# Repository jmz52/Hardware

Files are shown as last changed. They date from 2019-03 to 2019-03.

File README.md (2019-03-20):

# RAMPS-like shield for [black STM32F407VET6](https://wiki.stm32duino.com/index.php?title=STM32F407) board

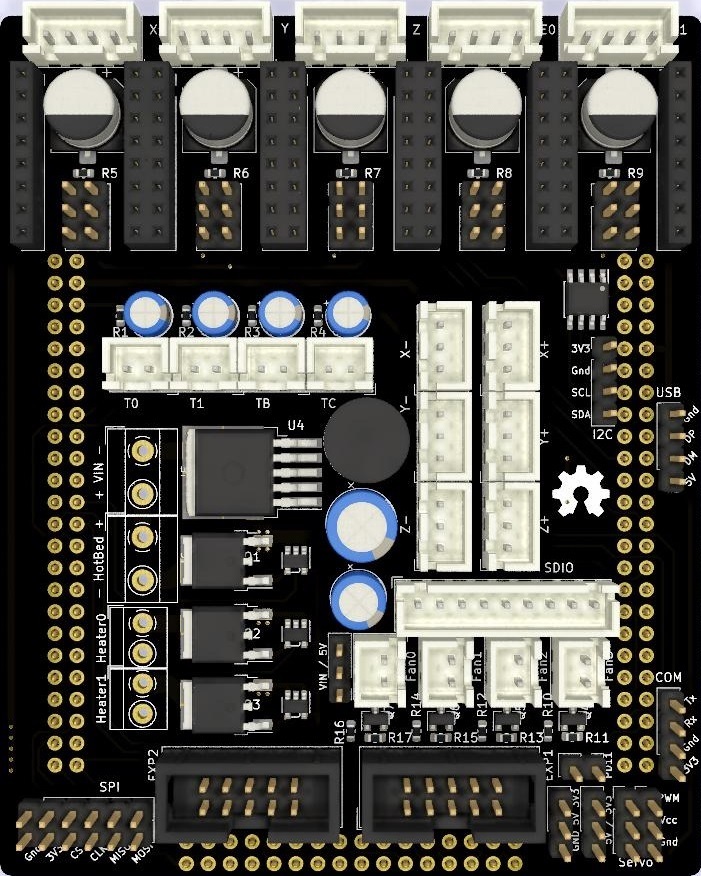
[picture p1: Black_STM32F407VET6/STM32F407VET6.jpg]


__Work-in-progress. Use with caution!__

First public release.
Corrected version of prototype board.

Changelog:
 - Updated pins names on 2x24 connectors and removed 3V3 to GND wire
 - Fixed broken E1_enable wire
 - Added missing wire between CLK pins in SPI connector

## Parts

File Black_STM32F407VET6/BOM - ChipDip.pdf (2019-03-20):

| количество | Ном. номер | цена | | название
Нагреватели | 3 | 9000087082 | 27 | 81 | IRLR8726PBF, Транзистор, N-канал 30В 85А [D-PAK]
| 3 | 9050000043 | 6 | 18 | SN74AHC1G125DBVR, Микросхема 1 Bus Buffer Gate 3-St SN [SOT-23-5]
Вентиляторы | 4 | 9000089114 | 10 | 40 | IRLML0030TRPBF, Транзистор, N-канал 30В 5.3А, [SOT-23]
| 4 | 9000079557 | 0.90 | 3.60 | 0.063Вт 0603 10 Ом, 1%, Чип резистор (SMD)
| 4 | 9000079736 | 0.90 | 3.60 | 0.063Вт 0603 10 кОм, 1%, Чип резистор (SMD)
5V | 1 | 949674977 | 290 | 290 | LM2596S-5.0/NOPB, Импульсный понижающий регулятор напряжения, 5В, 3А, 150кГц [TO-263-5]
| 1 | 9000355356 | 5 | 5 | SS14, Диод Шоттки 1A 40В [SMA / DO-214AC]
| 1 | 51810 | 38 | 38 | RLB0914-470KL, 47 мкГн,, Катушка индуктивности
| 1 | 9000261772 | 8 | | ECAP (К50-35 мини), 100 мкФ, 35 В, 8х7мм, Конденсатор электролитический алюминиевый миниатюрный
| 1 | 484555302 | 7 | | ECAP (К50-35), 220 мкФ, 35 В, 105°C, Конденсатор электролитический алюминиевый
Клеммники | 2 | 3017 | 19 | 38 | ED500V-02P, Клеммник 2-контактный, 5мм
| 2 | 37182 | 25 | 50 | ED350V-02P, Клеммник
Обвязка | 4 | 9000261763 | 5 | 20 | ECAP (К50-35 мини), 10 мкФ, 16 В, 4х7мм, Конденсатор электролитический алюминиевый миниатюрный
термисторов | 4 | 9000079728 | 0.90 | 3.60 | 0.063Вт 0603 4.7 кОм, 1%, Чип резистор (SMD)
Обвязка | 5 | 31139 | 20 | 100 | ECAP SMD, 100 мкФ, 25В, Конденсатор электролитический алюминиевый SMD | для 12 вольт
драйверов | 0 | 821121660 | 19 | 0 | ECAP SMD, 100 мкФ, 50В, Конденсатор электролитический алюминиевый SMD | для 24 вольт
| 5 | 9000079728 | 0.9 | 4.5 | 0.063Вт 0603 4.7 кОм, 1%, Чип резистор (SMD)
| 15 | 38729 | 5 | 75 | MJ-O-6 (DS1027-2 A), Джампер 2.54х6мм 2-контактный открытый
USB | 2 | 9000079564 | 0.90 | 1.80 | 0.063Вт 0603 22 Ом, 1%, Чип резистор (SMD)
I2C | 2 | 9000079728 | 0.90 | 1.80 | 0.063Вт 0603 4.7 кОм, 1%, Чип резистор (SMD)
SPI | 1 | 9000079728 | 0.90 | 0.90 | 0.063Вт 0603 4.7 кОм, 1%, Чип резистор (SMD)
EEPROM | 1 | 9060000150 | 12.00 | 12.00 | M24C64-WMN6TP, Энергонезависимая память, 64 кбит [SO-8]

Разъемы
EXP1/EXP2 | 2 | 62904 | 6 | 12 | BH-10 (DS1013-10S) (IDC-10MS), Вилка на плату прямая 10 конт. 2.54мм
2.54 | 1 | 29417 | 21 | 21 | PBD-40 (DS1023-2X20), Гнездо на плату 2.54мм 2х20 прямое
| 2 | 36056 | 30 | 60 | PBD-50 (DS1023-2x25), Гнездо на плату 2.54мм 2х25 прямое | 2x24 нет в наличии
| 2 | 32562 | 7 | 14 | PBS-8 (DS-1023 -1x 8), Гнездо на плату 2.54мм 1х8 прямое
| 4 | 25097 | 10 | 40 | PBD-16 (DS1023-2x8), Гнездо на плату 2.54мм 2х8 прямое
| 2 | 250743391 | 13 | 26 | PLD-40 (DS-1021- 2x20), Вилка штыревая 2.54мм 2х20 прямая тип1
| 1 | 39606 | 15 | 15 | PLS-40 (DS1021-1x40), Вилка штыревая 2.54мм 1х40 прямая тип1
2.50 | 5 | 33929 | 5 | 25 | CWF-4 (DS1069-4 M), Вилка на плату 2.50мм прямая закрытая
| 6 | 758365295 | 5 | 30 | CWF-3 (DS1069-3 M), Вилка на плату 2.50мм прямая закрытая
| 8 | 526261177 | 5 | 40 | CWF-2 (DS1069-2 M), Вилка на плату 2.50мм прямая закрытая
| 1 | 9000526340 | 2 | 2 | DS1069-9 MVW6 (CWF-9*) (WK-09*) (PW10-9-M*) (B9B-XH*), Вилка на плату 2,5мм 9 pin
| | | | 1 071.80

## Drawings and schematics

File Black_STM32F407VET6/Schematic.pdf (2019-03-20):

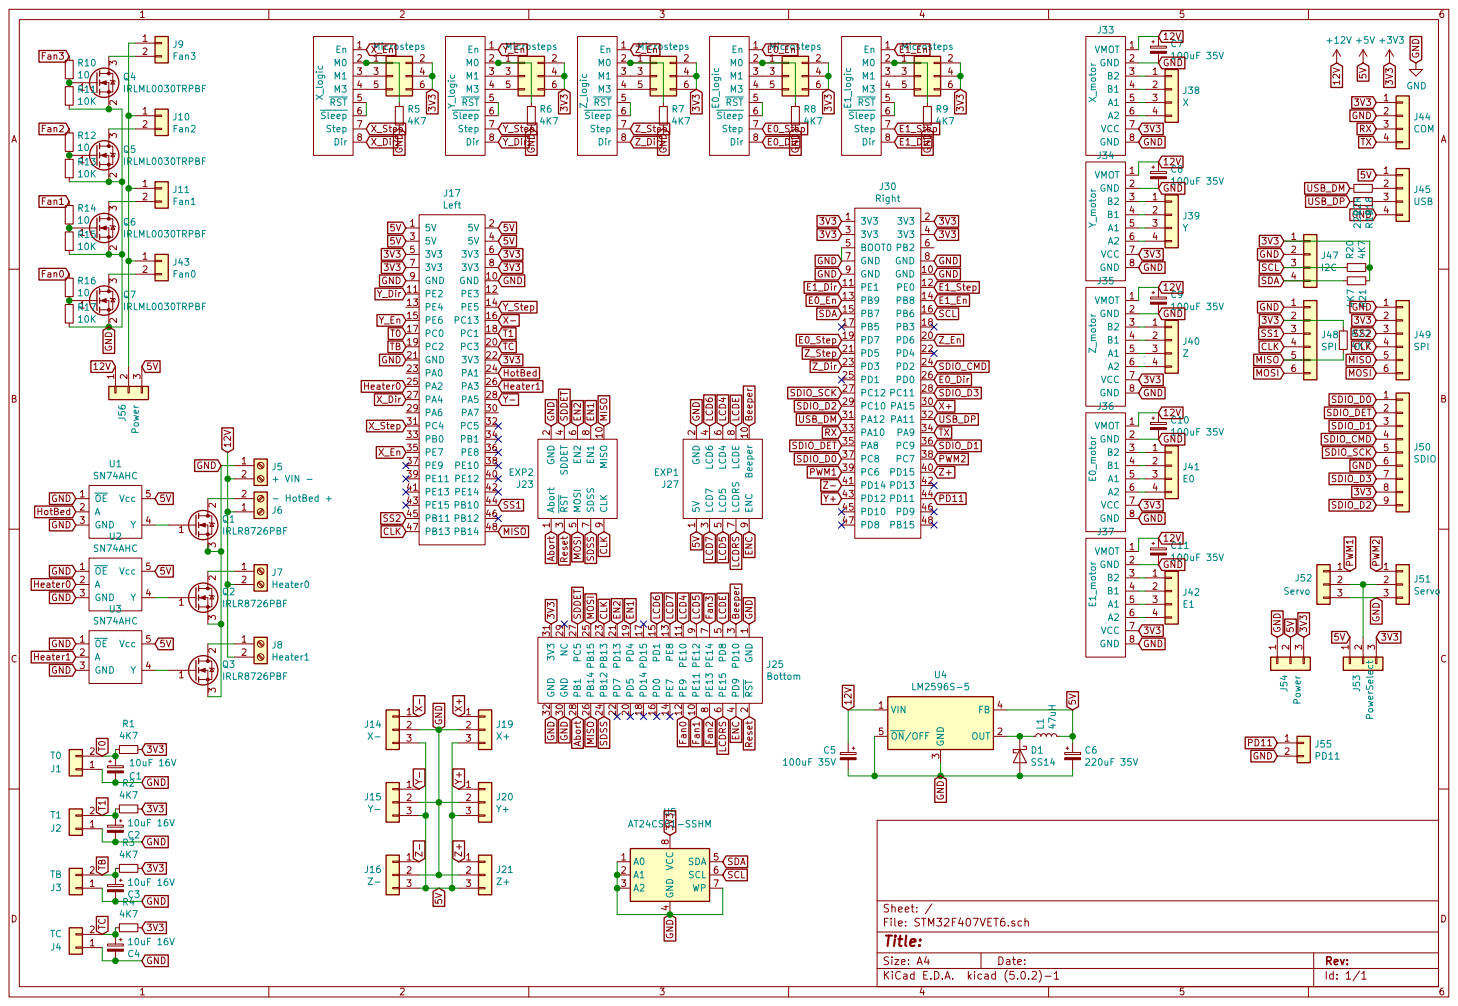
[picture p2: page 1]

3 J54 Power GND 5V3V3 MOSI MOSI MOSI A0 1 A1 2 A2 3 GND

8 U5 AT24CS01-SSHM GND 3V3 SCL SDA

4 SDA 5 SCL 6 WP 7 VCC

Id: 1/1 Title: File: STM32F407VET6.sch Sheet: /

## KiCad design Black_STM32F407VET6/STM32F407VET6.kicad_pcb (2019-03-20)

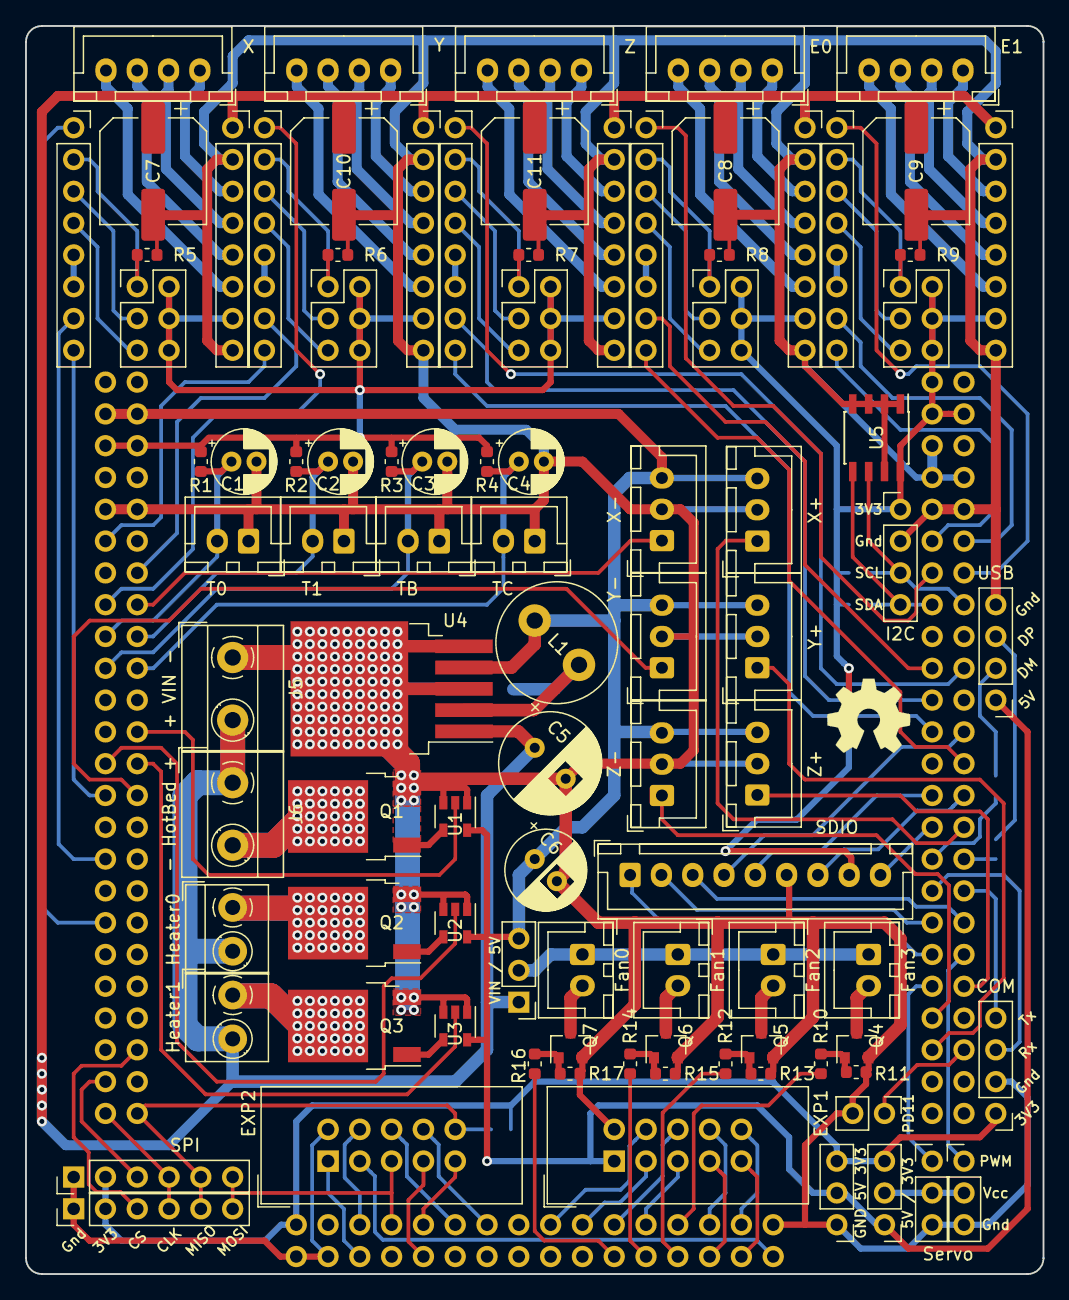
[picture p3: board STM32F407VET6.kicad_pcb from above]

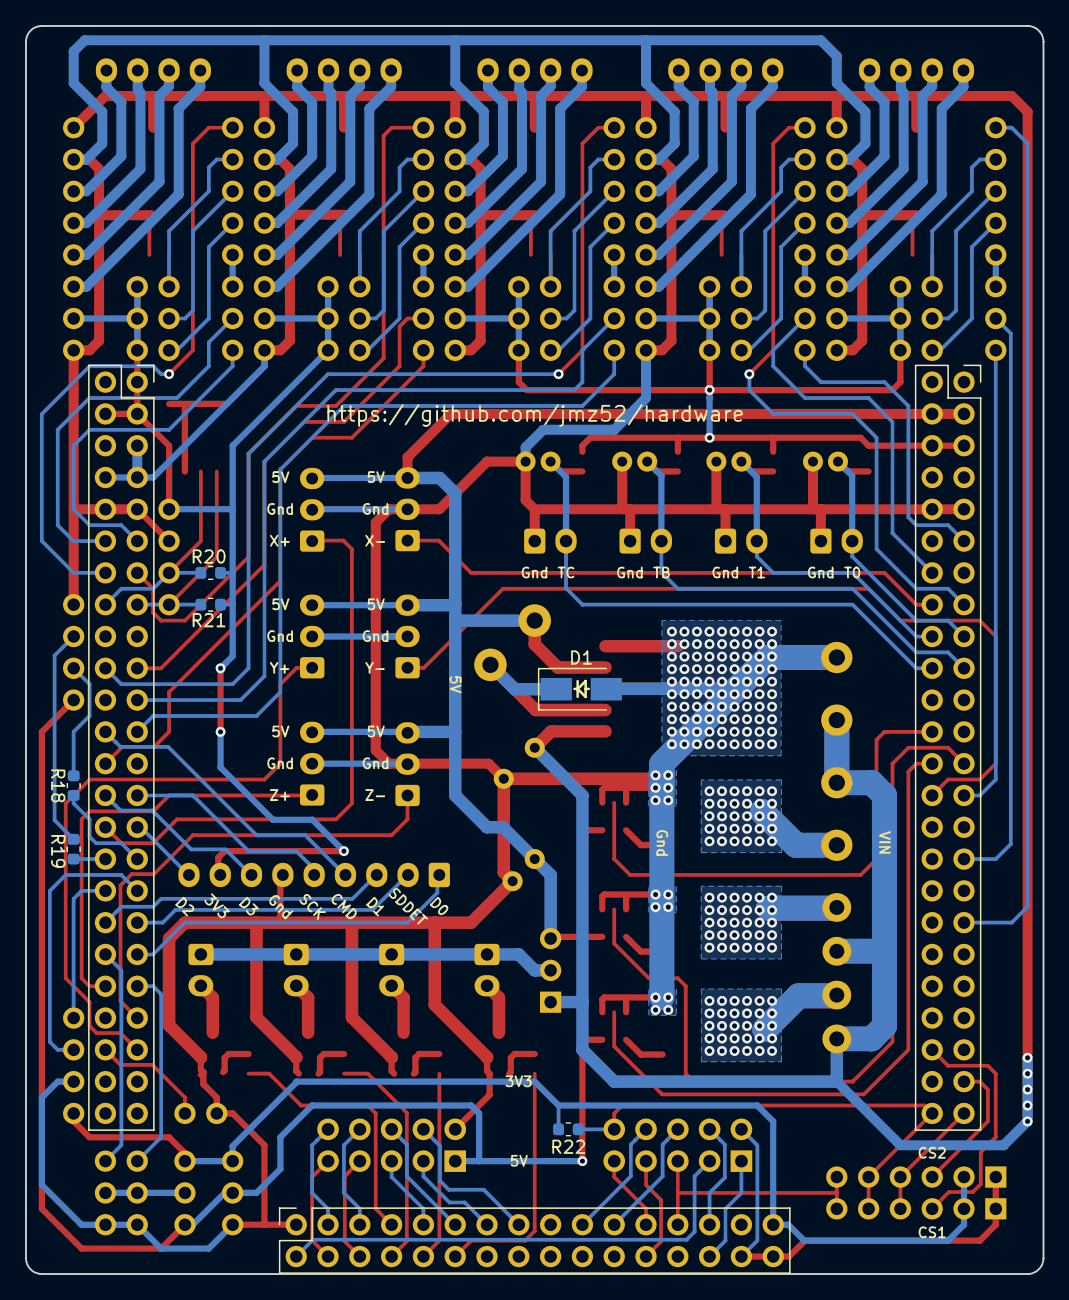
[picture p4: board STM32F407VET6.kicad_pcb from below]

Board: 2 copper layers, 81.3 x 99.7 mm, 102 parts (9 on the bottom side), 130 nets.

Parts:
C1, C2, C3, C4: 10uF 16V; CP_Radial_D5.0mm_P2.00mm
C5: 100uF 35V; CP_Radial_D8.0mm_P3.50mm
C6: 220uF 35V; CP_Radial_D6.3mm_P2.50mm
C7, C8, C9, C10, C11: 100uF 35V; CP_Elec_8x6.9
D1: SS14; D_SMA
J1: T0; JST_XH_B02B-XH-A_1x02_P2.50mm_Vertical
J2: T1; JST_XH_B02B-XH-A_1x02_P2.50mm_Vertical
J3: TB; JST_XH_B02B-XH-A_1x02_P2.50mm_Vertical
J4: TC; JST_XH_B02B-XH-A_1x02_P2.50mm_Vertical
J5: + VIN -; TerminalBlock_MetzConnect_Type055_RT01502HDWU_1x02_P5.00mm_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
J6: - HotBed +; TerminalBlock_MetzConnect_Type055_RT01502HDWU_1x02_P5.00mm_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
J7: Heater0; TerminalBlock_MetzConnect_Type059_RT06302HBWC_1x02_P3.50mm_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
J8: Heater1; TerminalBlock_MetzConnect_Type059_RT06302HBWC_1x02_P3.50mm_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
J9: Fan3; JST_XH_B02B-XH-A_1x02_P2.50mm_Vertical
J10: Fan2; JST_XH_B02B-XH-A_1x02_P2.50mm_Vertical
J11: Fan1; JST_XH_B02B-XH-A_1x02_P2.50mm_Vertical
J12: X_logic; PinSocket_1x08_P2.54mm_Vertical
J13, J22, J26, J29, J32: Microsteps; PinHeader_2x03_P2.54mm_Vertical
J14: X-; JST_XH_B03B-XH-A_1x03_P2.50mm_Vertical
J15: Y-; JST_XH_B03B-XH-A_1x03_P2.50mm_Vertical
J16: Z-; JST_XH_B03B-XH-A_1x03_P2.50mm_Vertical
J17: Left; PinSocket_2x24_P2.54mm_Vertical
J18: Y_logic; PinSocket_1x08_P2.54mm_Vertical
J19: X+; JST_XH_B03B-XH-A_1x03_P2.50mm_Vertical
J20: Y+; JST_XH_B03B-XH-A_1x03_P2.50mm_Vertical
J21: Z+; JST_XH_B03B-XH-A_1x03_P2.50mm_Vertical
J23: EXP2; IDC-Header_2x05_P2.54mm_Vertical
J24: Z_logic; PinSocket_1x08_P2.54mm_Vertical
J25: Bottom; PinSocket_2x16_P2.54mm_Vertical
J27: EXP1; IDC-Header_2x05_P2.54mm_Vertical
J28: E0_logic; PinSocket_1x08_P2.54mm_Vertical
J30: Right; PinSocket_2x24_P2.54mm_Vertical
J31: E1_logic; PinSocket_1x08_P2.54mm_Vertical
J33: X_motor; PinSocket_1x08_P2.54mm_Vertical
J34: Y_motor; PinSocket_1x08_P2.54mm_Vertical
J35: Z_motor; PinSocket_1x08_P2.54mm_Vertical
J36: E0_motor; PinSocket_1x08_P2.54mm_Vertical
J37: E1_motor; PinSocket_1x08_P2.54mm_Vertical
J38: X; JST_XH_B04B-XH-A_1x04_P2.50mm_Vertical
J39: Y; JST_XH_B04B-XH-A_1x04_P2.50mm_Vertical
J40: Z; JST_XH_B04B-XH-A_1x04_P2.50mm_Vertical
J41: E0; JST_XH_B04B-XH-A_1x04_P2.50mm_Vertical
J42: E1; JST_XH_B04B-XH-A_1x04_P2.50mm_Vertical
J43: Fan0; JST_XH_B02B-XH-A_1x02_P2.50mm_Vertical
J44: COM; PinHeader_1x04_P2.54mm_Vertical
J45: USB; PinHeader_1x04_P2.54mm_Vertical
J47: I2C; PinHeader_1x04_P2.54mm_Vertical
J48, J49: SPI; PinHeader_1x06_P2.54mm_Vertical
J50: SDIO; JST_XH_B09B-XH-A_1x09_P2.50mm_Vertical
J51, J52: Servo; PinHeader_1x03_P2.54mm_Vertical
J53: PowerSelect; PinHeader_1x03_P2.54mm_Vertical
J54, J56: Power; PinHeader_1x03_P2.54mm_Vertical
J55: PD11; PinHeader_1x02_P2.54mm_Vertical
L1: 47uH; L_Radial_D9.5mm_P5.00mm_Fastron_07HVP
Q1, Q2, Q3: Q_NMOS_GDS; TO-252-2
Q4, Q5, Q6, Q7: Q_NMOS_GSD; SOT-23
R1, R2, R3, R4, R5, R6, R7, R8, R9, R20, R21, R22: 4K7; R_0603_1608Metric
R10, R12, R14, R16: 10; R_0603_1608Metric
R11, R13, R15, R17: 10K; R_0603_1608Metric
R18, R19: 22R; R_0603_1608Metric
U1, U2, U3: SN74AHC; SOT-23-5
U4: LM2596S-5; TO-263-5_TabPin3
U5: AT24CS01-SSHM; SOIC-8_3.9x4.9mm_P1.27mm

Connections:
3V3: J13.2, J13.4, J13.6, J17.5, J17.6, J17.7, J17.8, J17.22, J22.2, J22.4, J22.6, J25.31, J26.2, J26.4, J26.6, J29.2, J29.4, J29.6, J30.1, J30.2, J30.3, J30.4, J32.2, J32.4, J32.6, J33.7, J34.7, J35.7, J36.7, J37.7, J44.1, J47.1, J48.2, J49.2, J50.8, J53.3, J54.3, R1.1, R2.1, R3.1, R4.1, R20.1, R21.2, R22.2, U5.8
5V: C6.1, J14.3, J15.3, J16.3, J17.1, J17.2, J17.3, J17.4, J19.3, J20.3, J21.3, J27.1, J45.1, J53.1, J54.2, J56.3, L1.2, U1.5, U2.5, U3.5, U4.4
12V: C5.1, C7.1, C8.1, C9.1, C10.1, C11.1, J5.2, J6.1, J7.2, J8.2, J33.1, J34.1, J35.1, J36.1, J37.1, J56.1, U4.1
Abort: J23.1, J25.28
Beeper: J25.3, J27.10
CLK: J17.47, J23.9, J25.23, J48.4, J49.4
E0_Dir: J28.8, J30.26
E0_En: J28.1, J30.13
E0_Step: J28.7, J30.19
E1_Dir: J30.11, J31.8
E1_En: J30.14, J31.1
E1_Step: J30.12, J31.7
EN1: J23.8, J25.19
EN2: J23.6, J25.21
ENC: J25.4, J27.9
Fan0: J25.12, R16.2
Fan1: J25.10, R14.2
Fan2: J25.8, R12.2
Fan3: J25.7, R10.2
GND: C1.2, C2.2, C3.2, C4.2, C5.2, C6.2, C7.2, C8.2, C9.2, C10.2, C11.2, D1.2, J1.1, J2.1, J3.1, J4.1, J5.1, J14.2, J15.2, J16.2, J17.9, J17.10, J17.21, J19.2, J20.2, J21.2, J23.2, J25.1, J25.30, J25.32, J27.2, J30.5, J30.7, J30.8, J30.9, J30.10, J33.2, J33.8, J34.2, J34.8, J35.2, J35.8, J36.2, J36.8, J37.2, J37.8, J44.2, J45.4, J47.2, J48.1, J49.1, J50.6, J51.3, J52.3, J54.1, J55.2, Q1.3, Q2.3, Q3.3, Q4.2, Q5.2, Q6.2, Q7.2, R5.1, R6.1, R7.1, R8.1, R9.1, R11.1, R13.1, R15.1, R17.1, U1.1, U1.3, U2.1, U2.3, U3.1, U3.3, U4.3, U4.5, U5.1, U5.2, U5.3, U5.4, U5.7
Heater0: J17.25, U2.2
Heater1: J17.26, U3.2
HotBed: J17.24, U1.2
LCD4: J25.11, J27.6
LCD5: J25.9, J27.5
LCD6: J25.15, J27.4
LCD7: J25.13, J27.3
LCDE: J25.5, J27.8
LCDRS: J25.6, J27.7
MISO: J17.48, J23.10, J25.26, J48.5, J49.5, R22.1
MOSI: J23.5, J25.25, J48.6, J49.6
unnamed: D1.1, L1.1, U4.2
unnamed: J6.2, Q1.2
unnamed: J7.1, Q2.2
unnamed: J8.1, Q3.2
unnamed: J9.2, Q4.3
unnamed: J9.1, J10.1, J11.1, J43.1, J56.2
unnamed: J10.2, Q5.3
unnamed: J11.2, Q6.3
unnamed: J12.2, J13.1, R5.2
unnamed: J12.3, J13.3
unnamed: J12.4, J13.5
unnamed: J12.5, J12.6
unnamed: J18.2, J22.1, R6.2
unnamed: J18.3, J22.3
unnamed: J18.4, J22.5
unnamed: J18.5, J18.6
unnamed: J24.2, J26.1, R7.2
unnamed: J24.3, J26.3
unnamed: J24.4, J26.5
unnamed: J24.5, J24.6
unnamed: J28.2, J29.1, R8.2
unnamed: J28.3, J29.3
unnamed: J28.4, J29.5
unnamed: J28.5, J28.6
unnamed: J31.2, J32.1, R9.2
unnamed: J31.3, J32.3
unnamed: J31.4, J32.5
unnamed: J31.5, J31.6
unnamed: J33.3, J38.1
unnamed: J33.4, J38.2
unnamed: J33.5, J38.3
unnamed: J33.6, J38.4
unnamed: J34.3, J39.1
unnamed: J34.4, J39.2
unnamed: J34.5, J39.3
unnamed: J34.6, J39.4
unnamed: J35.3, J40.1
unnamed: J35.4, J40.2
unnamed: J35.5, J40.3
unnamed: J35.6, J40.4
unnamed: J36.3, J41.1
unnamed: J36.4, J41.2
unnamed: J36.5, J41.3
unnamed: J36.6, J41.4
unnamed: J37.3, J42.1
unnamed: J37.4, J42.2
unnamed: J37.5, J42.3
unnamed: J37.6, J42.4
unnamed: J43.2, Q7.3
unnamed: J45.2, R18.2
unnamed: J45.3, R19.2
unnamed: J51.2, J52.2, J53.2
unnamed: Q1.1, U1.4
unnamed: Q2.1, U2.4
unnamed: Q3.1, U3.4
unnamed: Q4.1, R10.1, R11.2
unnamed: Q5.1, R12.1, R13.2
unnamed: Q6.1, R14.1, R15.2
unnamed: Q7.1, R16.1, R17.2
PD11: J30.44, J55.1
PWM1: J30.39, J52.1
PWM2: J30.38, J51.1
RX: J30.33, J44.3
Reset: J23.3, J25.2
SCL: J30.16, J47.3, R20.2, U5.6
SDA: J30.15, J47.4, R21.1, U5.5
SDDET: J23.4, J25.27
SDIO_CMD: J30.24, J50.4
SDIO_D0: J30.37, J50.1
SDIO_D1: J30.36, J50.3
SDIO_D2: J30.29, J50.9
SDIO_D3: J30.28, J50.7
SDIO_DET: J30.35, J50.2
SDIO_SCK: J30.27, J50.5
SDSS: J23.7, J25.24
SS1: J17.44, J48.3
SS2: J17.45, J49.3
T0: C1.1, J1.2, J17.17, R1.2
T1: C2.1, J2.2, J17.18, R2.2
TB: C3.1, J3.2, J17.19, R3.2
TC: C4.1, J4.2, J17.20, R4.2
TX: J30.34, J44.4
USB_DM: J30.31, R18.1
USB_DP: J30.32, R19.1
X+: J19.1, J30.30
X-: J14.1, J17.16
X_Dir: J12.8, J17.27
X_En: J12.1, J17.35
X_Step: J12.7, J17.31
Y+: J20.1, J30.43
Y-: J15.1, J17.28
Y_Dir: J17.11, J18.8
Y_En: J17.15, J18.1
Y_Step: J17.14, J18.7
Z+: J21.1, J30.40
Z-: J16.1, J30.41
Z_Dir: J24.8, J30.23
Z_En: J24.1, J30.20
Z_Step: J24.7, J30.21

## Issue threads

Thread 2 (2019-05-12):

C6

mr-miky, 2019-05-12:
There are a few things I wanted to tell you.

C6 does not need 35V since it is after a 5V regulator. 10 or 6.3 V are enough and I would put it Low Z and better polymeric type.
I would put in parallel 10uF mlcc X7R ...
As for LM2596 I would put a BIG warning to NOT use china chips because they are fakes and work at 50KHz instead of the 150Khz of the original ones. The result is a lot of outgoing ripples.
Mosfet drivers are not strictly necessary if you use modern mosfets, there are mosfets with VPon of 2.5V then you control them directly (you could insert a bypass). Add a 100nF bypass to each driver's power supply.
I would put a resistance and two diodes to protect the inputs of the limit switches, the stm32 is 5V compatible in ingrsso but it digests a 12V connected by mistake.
I would put a 500mA self-resetting fuse to protect the 5V they make at the limit switches and the probe ...

From experience I have learned not to trust end users ...

I started the development with the same 407Vte that you use and later I made a complete board all in one to replace it in a geeetech ..

[FanAndLimit-Fan,  limits and BLtouch.pdf](https://github.com/jmz52/Hardware/files/3170133/FanAndLimit-Fan.limits.and.BLtouch.pdf)
[HotAmdTemp-Hot and temperature.pdf](https://github.com/jmz52/Hardware/files/3170134/HotAmdTemp-Hot.and.temperature.pdf)
[psu-Power Supply.pdf](https://github.com/jmz52/Hardware/files/3170135/psu-Power.Supply.pdf)

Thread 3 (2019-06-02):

DRC未通过

skcks, 2019-06-02:
未连接项目有13个，请问作者还会继续完成吗

jmz52, 2019-06-07:
This is a shields for STM32F407 dev board.
All 'disconnected' wires on the shield are connected via main board.

skcks, 2019-06-07:
thanks,   understand now .  I already make some modification for it.

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

Closed 2019-06-07.

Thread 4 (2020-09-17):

help config marlin suport tft_spi ili9341 2.8 touch

minhngoc123, 2020-09-17:
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

hello,i want build marlin with stm32f407vet6 but i can't buid it .because when i build with vscode it show issues
no have spi tft config,only show
//=============================================================================
//=============================== Graphical TFTs ==============================
//=============================================================================

//
// FSMC display (MKS Robin, Alfawise U20, JGAurora A5S, REXYZ A1, etc.)
//
#define FSMC_GRAPHICAL_TFT

but build not complete
link marlin i dowload: https://github.com/jmz52/Marlin
you can send me link marlin support tft_spi for stmf407vet6 ,thank you so much

jmz52, 2020-09-17:
You need to use official repository - https://github.com/MarlinFirmware/Marlin
Enable `#define TFT_320x240_SPI` parameter in Configuration.h to use ili9341 SPI screen
Enable `#define TOUCH_SCREEN` parameter if you screen has touch panel

minhngoc123, 2020-09-17:
i dowload marlin : https://github.com/MarlinFirmware/Marlin
i configed :
#define MOTHERBOARD BOARD_BLACK_STM32F407VE
#define SERIAL_PORT 1
#define TFT_320x240_SPI
#define TFT_DRIVER AUTO
#define TOUCH_SCREEN
#if ENABLED(TOUCH_SCREEN)
  #define BUTTON_DELAY_EDIT  50 // (ms) Button repeat delay for edit screens
  #define BUTTON_DELAY_MENU 250 // (ms) Button repeat delay for menus

  #define TOUCH_SCREEN_CALIBRATION

  #define XPT2046_X_CALIBRATION 12316
  #define XPT2046_Y_CALIBRATION -8981
  #define XPT2046_X_OFFSET        -43
  #define XPT2046_Y_OFFSET        257
#endif
into file platformio.ini
[platformio]
src_dir      = Marlin
boards_dir   = buildroot/share/PlatformIO/boards
default_envs = STM32F407VE_black
include_dir  = Marlin
but i build not complete
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
tft_spi support stm32f407vet6 ? thank you

jmz52, 2020-09-17:
Missing pins are defining how you TFT and touch are connected.
Define them in pins file according to your schematic.

minhngoc123, 2020-09-17:
i use code from file robin nano and add to file black_stm32f407ve
code
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
#if HAS_SPI_TFT

  // Shared SPI TFT

  #define LCD_BACKLIGHT_PIN                 PD13

  #define TOUCH_CS_PIN                      PE14  // SPI1_NSS
  #define TOUCH_SCK_PIN                     PA5   // SPI1_SCK
  #define TOUCH_MISO_PIN                    PA6   // SPI1_MISO
  #define TOUCH_MOSI_PIN                    PA7   // SPI1_MOSI

  #define BTN_EN1                           PE8
  #define BTN_EN2                           PE11
  #define BTN_ENC                           PE13

  #define TFT_CS_PIN                        PD11
  #define TFT_SCK_PIN                       PA5
  #define TFT_MISO_PIN                      PA6
  #define TFT_MOSI_PIN                      PA7
  #define TFT_DC_PIN                        PD10
  #define TFT_RST_PIN                       PC6
  #define TFT_A0_PIN                  TFT_DC_PIN

  #define TFT_RESET_PIN                     PC6
  #define TFT_BACKLIGHT_PIN                 PD13

  #define TOUCH_BUTTONS_HW_SPI
  #define TOUCH_BUTTONS_HW_SPI_DEVICE          1

  #ifndef TFT_WIDTH
    #define TFT_WIDTH                        480
  #endif
  #ifndef TFT_HEIGHT
    #define TFT_HEIGHT                       320
  #endif

  #define LCD_READ_ID                       0xD3
  #define LCD_USE_DMA_SPI

#endif

minhngoc123, 2020-09-17:
can you send me file marlin was config for stm32f407vet6,thanks you
gmail: xiunhanbin96@gmail.com
thank you so much
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

minhngoc123, 2020-09-17:
please help me,thank you so much

jmz52, 2020-09-18:
@minhngoc123
It turns out that TFT SPI support is implemented for STM32F1xx only.
I've added some STM32F4xx specific code to address compilation errors, but I have no hardware to test it -  the STM32F407VE board installed in my printer is currently very busy and can't be removed.
I need to solder new shield for STM32F407VE board before I can test new code.

minhngoc123, 2020-09-19:
oh,i hope it come soon for stm32f407vet6
and stm32f1xx , that stm32f103rbt6 suport,
i have board : https://vi.aliexpress.com/item/32849464928.html
it support ?
i don't see config pin for stmf103rbt6 or stmf103rct6 . I only see CONFIG PIN FOR board robin nano ( stm32f103vet6)
thank you so much

minhngoc123, 2020-09-20:
a config board robin nano v2
i change code into file platfom.ini
i choose chip stm32f103rct6 and build
It seems that it suffers from insufficient memory
but stm32f103vet6 build ok
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

minhngoc123, 2020-09-20:
i hope tft_spi for stmf103rct6 and stm32f407vet6
i hope frome you

jmz52, 2020-09-22:
I've uploaded updated code with support for Updated code with SPI TFT support for SPI TFT on STM32F4.
It works just fine on my black STM32F407VE with ST77796 screen.

Technically it is possible to compile Marlin for EZT3D board.
There are two problems with this board
- board's native screen 128x128 TFT on ST7735 driver is not supported in Marlin yet
- MCU only has 128KB flash and this board is used in EZT-T1 delta printers. There is not enough flash to fit all features needed for delta printer.

minhngoc123, 2020-09-23:
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

minhngoc123, 2020-09-23:
i try dowload marlin on github.com/jmz52/marlin but i dont see tft_spi
and  i try dowload marlin https://github.com/MarlinFirmware/Marlin
and i config board stm32f407_black but into file pin_stm32f407vet6_black no have config tft
and i coppycode mks robin nano v2 add it issue
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
i try define com port 1 and 2
you can upload file config and file pin for stm32f407 use hardware : https://github.com/jmz52/Hardware
                                                                     THANK YOU SO MUCH !
and code file black_stm32f407ve.h
/**
 * Marlin 3D Printer Firmware
 * Copyright (c) 2020 MarlinFirmware [https://github.com/MarlinFirmware/Marlin]
 *
 * Based on Sprinter and grbl.
 * Copyright (c) 2011 Camiel Gubbels / Erik van der Zalm
 *
 * This program is free software: you can redistribute it and/or modify
 * it under the terms of the GNU General Public License as published by
 * the Free Software Foundation, either version 3 of the License, or
 * (at your option) any later version.
 *
 * This program is distributed in the hope that it will be useful,
 * but WITHOUT ANY WARRANTY; without even the implied warranty of
 * MERCHANTABILITY or FITNESS FOR A PARTICULAR PURPOSE.  See the
 * GNU General Public License for more details.
 *
 * You should have received a copy of the GNU General Public License
 * along with this program.  If not, see <https://www.gnu.org/licenses/>.
 *
 */
#pragma once

/**
 * STM32F407VET6 with RAMPS-like shield
 * 'Black' STM32F407VET6 board - https://www.stm32duino.com/viewtopic.php?t=485
 * Shield - https://github.com/jmz52/Hardware
 */

#if !defined(STM32F4) && !defined(STM32F4xx)
  #error "Oops! Select an STM32F4 board in 'Tools > Board.'"
#elif HOTENDS > 2 || E_STEPPERS > 2
  #error "Black STM32F4VET6 supports up to 2 hotends / E-steppers."
#endif

#ifndef BOARD_INFO_NAME
  #define BOARD_INFO_NAME "Black STM32F4VET6"
#endif

#define DEFAULT_MACHINE_NAME "STM32F407VET6"

//#define I2C_EEPROM
#define DISABLE_DEBUG

//
// EEPROM
//
//#define FLASH_EEPROM_EMULATION
//#define SDCARD_EEPROM_EMULATION

#if EITHER(NO_EEPROM_SELECTED, I2C_EEPROM)
  #define I2C_EEPROM                              // EEPROM on I2C-0
  #define MARLIN_EEPROM_SIZE              0x1000  // 4KB
#endif

//
// Note: MKS Robin board is using SPI2 interface.
//
//#define SPI_MODULE                           2
#define ENABLE_SPI2

//
// Limit Switches
//
#define X_DIAG_PIN                          PA15
#define Y_DIAG_PIN                          PA12
#define Z_DIAG_PIN                          PA11
#define E0_DIAG_PIN                         PC4
#define E1_DIAG_PIN                         PE7

#define X_STOP_PIN                          PA15
#define Y_STOP_PIN                          PA12
#define Z_MIN_PIN                           PA11
#define Z_MAX_PIN                           PC4

//
// Steppers
//
#define X_ENABLE_PIN                        PE4
#define X_STEP_PIN                          PE3
#define X_DIR_PIN                           PE2
#ifndef X_CS_PIN
  #define X_CS_PIN                          PD5
#endif

#define Y_ENABLE_PIN                        PE1
#define Y_STEP_PIN                          PE0
#define Y_DIR_PIN                           PB9
#ifndef Y_CS_PIN
  #define Y_CS_PIN                          PD7
#endif

#define Z_ENABLE_PIN                        PB8
#define Z_STEP_PIN                          PB5
#define Z_DIR_PIN                           PB4
#ifndef Z_CS_PIN
  #define Z_CS_PIN                          PD4
#endif

#define E0_ENABLE_PIN                       PB3
#define E0_STEP_PIN                         PD6
#define E0_DIR_PIN                          PD3
#ifndef E0_CS_PIN
  #define E0_CS_PIN                         PD9
#endif

#define E1_ENABLE_PIN                       PA3
#define E1_STEP_PIN                         PD15
#define E1_DIR_PIN                          PA1
#ifndef E1_CS_PIN
  #define E1_CS_PIN                         PD8
#endif

//
// Software SPI pins for TMC2130 stepper drivers
//
#if ENABLED(TMC_USE_SW_SPI)
  #ifndef TMC_SW_MOSI
    #define TMC_SW_MOSI                     PD14
  #endif
  #ifndef TMC_SW_MISO
    #define TMC_SW_MISO                     PD1
  #endif
  #ifndef TMC_SW_SCK
    #define TMC_SW_SCK                      PD0
  #endif
#endif
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
jmz52, 2020-09-23:
Sorry, forgot to specify branch with updated code
https://github.com/jmz52/Marlin/tree/tft_and_touch_N2

minhngoc123, 2020-09-24:
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
 THANK YOU SO MUCH
but i have issues main board have port com port 5,  but i can't connect to host .
file config  detault,i don't change it

I'm sorry to bother you so much ,i can't fix it
THANK YOU SO MUCH
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

jmz52, 2020-09-24:
It is a known issue with no USB reenumeration on MCU reset.
You need to power board from external power supply and connect USB cable once firmware is running.

jmz52, 2020-09-24:
Black F407VE uses MCU's battery backed ram to emulate EEPROM. You need to install battery if you want to use this feature.

minhngoc123, 2020-09-24:
thanks you so much,
and i have tft ili9341 2,8 with touch screen
how to calibration touch screen
i see in code :
#define TOUCH_SCREEN_CALIBRATION

  #define TOUCH_CALIBRATION_X   16692
  #define TOUCH_CALIBRATION_Y   11328
  #define TOUCH_OFFSET_X        -14
  #define TOUCH_OFFSET_Y        -20
  #define TOUCH_ORIENTATION     TOUCH_LANDSCAPE
I don't know where these figures are
and are you use facebook?
THANKS YOU SO MUCH

jmz52, 2020-09-24:
Two ways to start built-in calibration:
- Connect to COM port at type M995 command.
- Press and hold (for 3 seconds if I recall correctly) non-interactive area on main screen.

Once calibration is completed , the calibration data will be displayed on COM port, so you can add them to your configuration file.
Alternatively you can save calibration data along with other settings to EEPROM using M50x commands

minhngoc123, 2020-09-24:
thank you so much

minhngoc123, 2020-09-25:
i try use external power supply and connect USB ,
the firt i use 5v power from samsung 2a changer ,led s2 flashes slow ,i connect usb com port but i can't connec to host,
in spite of device manager show usb serial com 5
i try use power 2s 7.4v and led flash off quickly,i connect usb
https://drive.google.com/file/d/1NpUpZnS2FaP-yLThtrtLvi6a4QAAWR6k/view?usp=drivesdk
but ic power die and hot ,i seach schematic board i see board not have dioze protect usb power

minhngoc123, 2020-10-18:
In the Future in the future, will stmf407 support ftf_lvgl_spi

Closed 2020-10-30.

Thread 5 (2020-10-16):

Enstop to 5v or 3.3v

minhngoc123, 2020-10-16:
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
I see schematic.i found out that the enstop is connected to 5v. will it damage stm32

jmz52, 2020-10-16:
STM32 GPIOs are 5V tolerant.
5V is used for compatibility with active endstop.
Passive endstops usually connects signal pin with ground and do not use 5v line at all.

minhngoc123, 2020-10-17:
Thank you so much

Closed 2020-10-30.
